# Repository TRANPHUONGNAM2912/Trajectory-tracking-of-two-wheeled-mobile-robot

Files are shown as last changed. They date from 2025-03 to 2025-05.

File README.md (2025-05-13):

<<<<<<< HEAD
# Điều Khiển Bám Quỹ Đạo Cho Robot Di Động Hai Bánh

## Tổng Quan
Dự án này tập trung vào việc thiết kế và đánh giá các bộ điều khiển bám quỹ đạo cho robot di động hai bánh vi sai. Nghiên cứu bao gồm việc phát triển và so sánh hiệu suất của nhiều phương pháp điều khiển như PID, SMC (Điều Khiển Trượt), ASMC (Điều Khiển Trượt Thích Nghi), Fuzzy Logic và Neural Network. Các bộ điều khiển được mô phỏng trong môi trường MATLAB/Simulink và sau đó được triển khai trên phần cứng thực tế thông qua mã nhúng C/C++ trên ESP32.

## Nội Dung Dự Án
- Mô hình hóa động học và động lực học của robot di động hai bánh vi sai
- Thiết kế các bộ điều khiển bám quỹ đạo:
  - Bộ điều khiển PID cổ điển
  - Bộ điều khiển trượt (SMC)
  - Bộ điều khiển trượt thích nghi (ASMC)
  - Bộ điều khiển logic mờ (Fuzzy Logic)
  - Bộ điều khiển mạng nơ-ron (Neural Network)
- Mô phỏng sử dụng MATLAB/Simulink
- Thiết kế mô hình phần cứng trên Solidworks
- Triển khai nhúng sử dụng ESP32
- So sánh hiệu suất giữa kết quả mô phỏng và thực nghiệm

## Cấu Trúc Thư Mục
- `Embedded_code/`: Chứa tất cả các bộ điều khiển cho ESP32
  - `NeuralNetwork.ino`: Triển khai bộ điều khiển mạng nơ-ron
  - `SMC.ino`: Triển khai bộ điều khiển trượt
  - `ASMC.ino`: Triển khai bộ điều khiển trượt thích nghi
  - `Fuzzy.ino`: Triển khai bộ điều khiển logic mờ
  - `PID_backstepping.ino`: Triển khai bộ điều khiển PID với backstepping
  - `GUI_CAR.py`: Giao diện Python để điều khiển và giám sát robot
- `MATLAB/`: Chứa các mô hình mô phỏng cho tất cả các bộ điều khiển
  - `NeuralNetwork/`: Mô phỏng bộ điều khiển mạng nơ-ron
  - `SMC/`: Mô phỏng bộ điều khiển trượt
  - `ASMC/`: Mô phỏng bộ điều khiển trượt thích nghi
  - `Fuzzy/`: Mô phỏng bộ điều khiển logic mờ
  - `PID/`: Mô phỏng bộ điều khiển PID
- `Solidworks/`: Chứa các mô hình CAD 3D của robot
- `docs/`: Tài liệu dự án và các bài báo nghiên cứu
  - `NeuralNetwork.pdf`: Tài liệu về bộ điều khiển mạng nơ-ron
  - `ITCA2024_NeuralNetwork.pdf`: Bài báo nghiên cứu về triển khai mạng nơ-ron
  - `VCCA2024_Fuzzy.pdf`: Bài báo nghiên cứu về triển khai logic mờ

## Yêu Cầu Phần Mềm
- MATLAB R2021B (hoặc cao hơn)
- Arduino IDE 2.xx (để lập trình ESP32)
- Solidworks 2022
- Python 3.x (cho ứng dụng giao diện)

## Yêu Cầu Phần Cứng
- Vi điều khiển ESP32
- Bộ điều khiển động cơ
- Động cơ DC có bộ mã hóa
- Khung cơ khí (theo thiết kế Solidworks)
- Nguồn điện

## Hướng Dẫn Cài Đặt
1. **Cài Đặt ESP32:**
   - Cài đặt board ESP32 của Espressif (phiên bản 2.0.17) trong Arduino IDE
   - Mở một trong các file điều khiển từ thư mục `Embedded_code/` trong Arduino IDE
   - Cập nhật SSID và mật khẩu WiFi trong mã
   - Tải mã lên ESP32

2. **Cài Đặt Giao Diện:**
   - Kết nối ESP32 và máy tính đến cùng một mạng WiFi (2.4GHz)
   - Ghi lại địa chỉ IP do ESP32 cung cấp sau khi kết nối
   - Cập nhật biến `ip_address` trong file `GUI_CAR.py`
   - Chạy ứng dụng giao diện Python

3. **Vận Hành:**
   - Sử dụng giao diện để bắt đầu/dừng robot
   - Giám sát hiệu suất và khả năng bám quỹ đạo trong thời gian thực

## Video Demo
- Xem demo: [Điều Khiển Bám Quỹ Đạo Cho Robot Di Động Hai Bánh](https://www.youtube.com/watch?v=6Xz11GfAjuo&t=38s)

## Lưu Ý Quan Trọng
- ESP32 và laptop phải kết nối cùng một mạng WiFi 2.4GHz
- Đảm bảo cài đặt tất cả các thư viện cần thiết cho ESP32 (WiFi, WebServer, MatrixMath)
- Nên giám sát mức pin trong quá trình hoạt động

## Giấy Phép
Dự án này được phân phối theo giấy phép MIT. Xem file LICENSE để biết thêm chi tiết.

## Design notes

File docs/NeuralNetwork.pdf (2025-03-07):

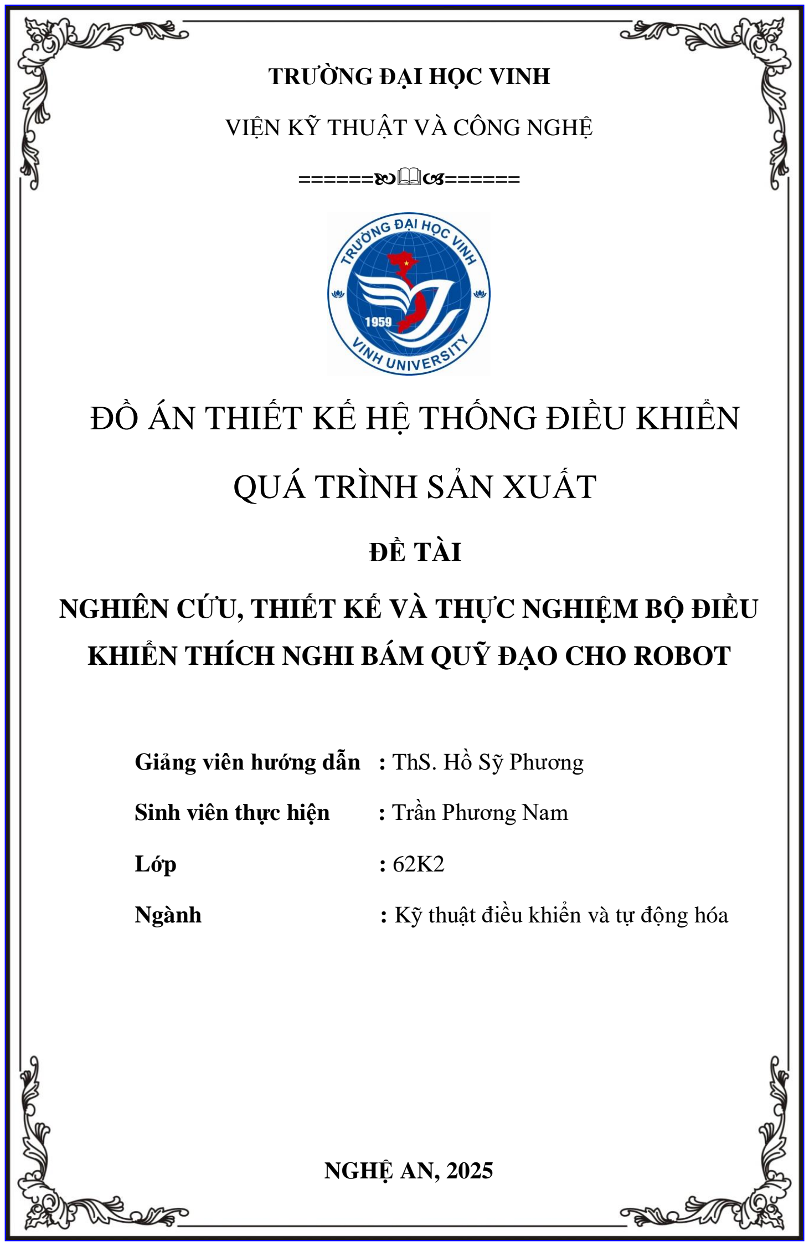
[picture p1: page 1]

TRƯỜNG ĐẠI HỌC VINH

VIỆN KỸ THUẬT VÀ CÔNG NGHỆ

============

## ĐỒ ÁN THIẾT KẾ HỆ THỐNG ĐIỀU KHIỂN

## QUÁ TRÌNH SẢN XUẤT

### ĐỀ TÀI

### NGHIÊN CỨU, THIẾT KẾ VÀ THỰC NGHIỆM BỘ ĐIỀU

### KHIỂN THÍCH NGHI BÁM QUỸ ĐẠO CHO ROBOT

Giảng viên hướng dẫn : ThS. Hồ Sỹ Phương

Sinh viên thực hiện | : Trần Phương Nam
Lớp | : 62K2
Ngành | : Kỹ thuật điều khiển và tự động hóa

NGHỆ AN, 2025

TRƯỜNG ĐẠI HỌC VINH | CỘNG HÒA XÃ HỘI CHỦ NGHĨA VIỆT NAM
VIỆN KT&CN | Độc lập – Tự do – Hạnh phúc

ĐỀ CƯƠNG THỰC HIỆN ĐỒ ÁN

Họ và tên sinh viên: Trần Phương Nam – 215752021610076

Ngành: Kỹ thuật điều khiển và tự động hóa

Đề tài: Nghiên cứu, thiết kế và thực nghiệm bộ điều khiển bám quỹ đạo cho robot.

### 1. Nhiệm vụ:

- Tìm hiều và xác định nội dung đồ án.
- Nghiên cứu mô hình toán học, động học, động lực học.
- Thiết kế bộ điều khiển, mô phỏng kiểm chứng bằng Matlab Simulink
- Lập trình, tiến hành thực nghiệm cho mô hình.
- Đánh giá kết quả thực nghiệm.
- Kết luận và hướng phát triển.

### 2. Ngày giao đồ án: Ngày 1 Tháng 9 năm 2024

### 3. Ngày hoàn thành đồ án: Ngày 10 Tháng 01 Năm 2025

Người hướng dẫn: ThS. Hồ Sỹ Phương

Nghệ An, Ngày ... Tháng ... Năm 202..

TRƯỞNG BỘ MÔN | NGƯỜI HƯỚNG DẪN

TRƯỜNG ĐẠI HỌC VINH | CỘNG HÒA XÃ HỘI CHỦ NGHĨA VIỆT NAM
VIỆN KT&CN | Độc lập – Tự do – Hạnh phúc BẢN TỰ ĐÁNH GIÁ

Nhóm trưởng: Trần Phương Nam

Đề tài: Nghiên cứu, thiết kế và thực nghiệm bộ điều khiển bám quỹ đạo cho robot.

| Phần đánh giá

Nghệ An, Ngày Tháng 01 Năm 2025 NHÓM TRƯỞNG

TT | Họ và tên MSSV | Nội dụng thực hiện | Kết quả | Đánh giá(%) | Ghi chú
1 | Trần Phương Nam 215752021610076 | - Nghiên cứu mô phỏng - Lập trình cho Robot -Thực nghiệm và tối ưu thuật toán | Hoàn thành | 100% | Nhóm trưởng

TRƯỜNG ĐẠI HỌC VINH | CỘNG HÒA XA HỘI CHỦ NGHĨA VIỆT NAM
VIỆN KT&CN | Độc lập – Tự do – Hạnh phúc

NHẬN XÉT CỦA NGƯỜI HƯỚNG DẪN

Họ và tên sinh viên: Trần Phương Nam – 215752021610076

Ngành: Kỹ thuật điều khiển và tự động hóa

Đề tài: Nghiên cứu, thiết kế và thực nghiệm bộ điều khiển bám quỹ đạo cho robot.

Nhận xét chung:

Phần đánh giá

TT | Họ và tên MSSV | Nội dụng thực hiện | Kết quả | Đánh giá(%) | Ghi chú
1 | Trần Phương Nam 215752021610076 | - Nghiên cứu mô phỏng - Lập trình cho Robot - Thực nghiệm và tối ưu thuật toán | | | Nhóm trưởng
- Ý thức thực hiện: |
- Nội dung thực hiện: |
- Hình thức trình bày: |
Tổng hợp kết quả( điểm bằng số và bằng chữ):
+Điểm chuyên cần: |
+Điểm giữa kỳ: |

Nghệ An, Ngày ... Tháng 01 Năm 2025 NGƯỜI HƯỚNG DẪN

MỤC LỤC

DANH MỤC HÌNH ẢNH

Hình 3.7 Tham số điều khiển được huấn luyện và chỉnh định theo điều kiện thực nghiệm

TÓM TẮT

Robot di động 2 bánh vi sai (DDMR) đã trở thành một nền tảng phổ biến trong các

ứng dụng công nghiệp và dịch vụ nhờ tính linh hoạt, dễ thiết kế và triển khai trong nhiều

môi trường khác nhau. Tuy nhiên, việc điều khiển chính xác quỹ đạo của robot trong thực

tế vẫn là một bài toán khó do sự xuất hiện của nhiễu và các yếu tố môi trường thay đổi

liên tục [1][2]. Các phương pháp điều khiển truyền thống như PID hay điều khiển trượt

(SMC) thường được sử dụng nhờ tính hiệu quả trong các tình huống tiêu chuẩn, nhưng

chúng lại phụ thuộc nhiều vào mô hình động lực học chính xác. Điều này dẫn đến hạn

chế trong việc xử lý các yếu tố bất định và biến đổi không dự đoán trước, đặc biệt khi hệ

thống hoạt động trong môi trường phức tạp [3][4].

Để vượt qua những thách thức này, mạng nơ-ron nhân tạo (ANN) đã được triển

khai trong các bộ điều khiển robot như một công cụ mạnh mẽ, nhờ khả năng học tập và

thích nghi với các điều kiện thay đổi. ANN có thể giảm sự phụ thuộc vào các mô hình

toán học phức tạp, cho phép robot tự động điều chỉnh các tham số điều khiển, từ đó cải

thiện hiệu suất và độ chính xác trong việc bám quỹ đạo [5][6]. Nhiều nghiên cứu đã

chứng minh ANN có khả năng ước lượng chính xác các tham số hệ thống, đồng thời xử

lý hiệu quả các yếu tố bất định và nhiễu động trong môi trường thực tế [7][8]. Tuy nhiên,

đa số các nghiên cứu này chỉ dừng lại ở mức mô phỏng, chưa được kiểm chứng đầy đủ

trên các hệ thống thực tế [9].

Trong đồ án này, nhóm thực hiện phát triển và kiểm chứng một bộ điều khiển

thích nghi dựa trên mạng nơ-ron dành cho DDMR. Bộ điều khiển được thiết kế để tự học

và điều chỉnh tham số động học chưa biết, từ đó tối ưu hóa khả năng bám quỹ đạo trong

môi trường có nhiễu và yếu tố biến động. Đặc biệt, bộ điều khiển không chỉ giúp giảm

thiểu sai số mà còn đảm bảo độ ổn định cao ngay cả trong điều kiện hoạt động khắc

nghiệt [10]. Kết quả thực nghiệm đã chứng minh bộ điều khiển đạt hiệu suất vượt trội so

với các phương pháp truyền thống, với khả năng duy trì tính chính xác và ổn định của hệ

thống trong nhiều tình huống khác nhau [11].

Nội dung đồ án được tổ chức thành 4 phần chính. Phần 1 trình bày chi tiết quá

trình mô hình hóa robot. Phần 2 đi sâu vào mô tả bộ điều khiển dựa trên mạng nơ-ron, tập

trung vào cách thức tự động chỉnh định tham số. Phần 3 phân tích kết quả thực nghiệm,

minh chứng hiệu quả của bộ điều khiển trong điều kiện thực tế. Cuối cùng, phần 4 kết luận và đề xuất các hướng phát triển trong tương lai, nhấn mạnh tiềm năng ứng dụng của

đồ án trong các hệ thống tự động hóa khác [12].

CHƯƠNG 1. MÔ HÌNH HOÁ ROBOT

### 1.1 Mô hình toán học

Cấu trúc của robot di động được thiết kế có bốn bánh xe. Hai bánh xe ở giữa là 2

bánh chủ động, được điều khiển bởi hai động cơ DC. Một bánh xe phía trước và sau thân

robot là 2 bánh thụ động. Cấu trúc robot được thể hiện trong Hình 1.1. Điểm G là trọng

tâm robot, 2 động cơ được sắp xếp đồng trục.

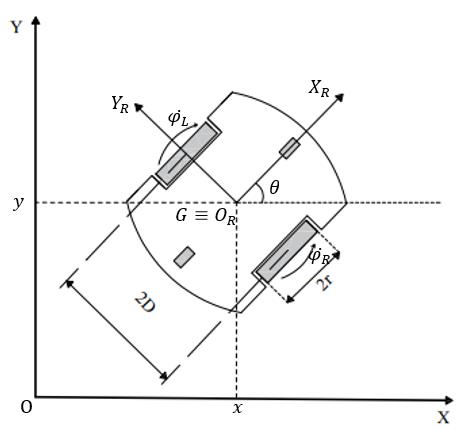
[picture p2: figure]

Hình 1.1 Cấu trúc robot di động

Hệ toạ độ tại điểm G{ORXRYR} gắn trên thân robot được gọi là hệ toạ độ robot

hoặc hệ toạ cục bộ vì hệ toạ độ này được dịch chuyển theo chuyển động của robot di

động. Hệ toạ độ còn lại {OXY} được gọi là hệ toạ độ quán tính hay hệ toạ độ cố định,

được sử dụng khi làm việc trên vị trí của robot. Hai hệ toạ độ này lần lượt được biểu diễn

như sau:

[ | ]
[ | ]

T
R | r | r | r
| | T
q | x y
q | x y

θ

| θ

ì
ï =
í
ï = î

(1)

Một ma trận biến đổi Rot(θ) được sử dụng để chuyển đổi giữa hệ toạ độ cố định

và hệ toạ độ robot:

1
( ) | ( ) R | R q | Rot | q | q Rot | q θ | θ
= | Þ = | (2)

Trong đó:

1

| cos | sin | 0
( ) | sin | cos | 0
| 0 | 0 | 1

Rot

| θ | θ
θ | θ | θ

é | ù -
ê | | ú
=
ê | | ú
ê | ú ë | û

(3)

### 1.2 Mô hình động học

Động học của robot liên quan đến mối quan hệ giữa vị trí, vận tốc, gia tốc và các

cấu trúc vật lý của nó. Bằng cách thay đổi vận tốc của hai bánh xe, quỹ đạo của robot có

thể thay đổi.
, φφR L

lần lượt là vận tốc quay của bên phải và bên trái. Ta có:

R | R
L | L
V | r
V | r φ
| φ

=
=

(4)

VR
và

VL

là vận tốc tuyến tính bánh xe phải và trái. Với bất ký trường hợp nào, v

và
ω

có thể được tính như sau:

( | )
2
( | )
2
R | L
R | L
V | V
v

V V D
ω

+
=
=

(5)

Từ (3) và (4), mối quan hệ vận tốc giữa hai toạ độ được biểu diễn như sau:

( | ) cos
2
| | cos | 0
( | )sin | sin | 0
2
0 | 1 ( | )

2

R | L
R | L
R | L
V | V

x
V | V | v
y

V V
D

θ
θ
θ | θ
ω
θ
é | ù +
ê | ú éù ê | ú é | ù êú | + | éù ê | ú ê | ú
= | = êú | êú ê | ú ê | úëû êú ê | ú ê | ú ëû | ë | û -
ê | ú ê | ú ë | û

(6)

Mô hình động học thuận của robot có thể được miêu tả như sau:

cos | 0
sin | 0 | ( ) ( )
0 | 1

x
v
y | S q V t

θ
θ
ω
θ
éù é | ù êú | éù ê | ú
= | = êú | êú ê | úëû êú ê | ú ëû ë | û

(7)

### 1.3 Mô hình động lực học

Phân tích động lực học của robot có thể được định nghĩa là kiểm tra mối quan hệ

giữa độ lớn mô-men xoắn hoặc độ lớn lực tác dụng lên bánh xe bởi bộ truyền động, vị trí,

vận tốc và gia tốc của robot theo thời gian. Sự khác biệt giữa mô hình động lực học và mô hình động học là mô hình động học chỉ xem xét chuyển động với các quan hệ hình

học chi phối hệ thống mà không xem xét các lực tác động đến chuyển động.

Theo [12], mô hình động lực học tính được như sau:

( ) | ( , ) | ( ) | ( )
( ) | ( )
M q q V q q q F q | G q | d
B q | A q τ

τ

τ | λ
+ | + | + | +
= | -

(8)

q, q˙ và q¨ lần lượt chỉ định các vectơ vị trí, vận tốc và gia tốc tương ứng. M(q) là

ma trận quán tính xác định dương đối xứng, V(q, q˙ ) là ma trận hướng tâm và Coriolis,

G(q) là lực hấp dẫn vectơ, τd biểu thị các nhiễu hoặc nhiễu không xác định giới hạn, bao

gồm cả động lực học phi cấu trúc không được mô hình hóa, B(q) là ma trận biến đổi đầu

vào, τ là vectơ mô-men xoắn đầu vào, A

τ
(q) là ma trận được liên kết với các ràng buộc

và λ là vectơ của các lực ràng buộc. Bỏ qua lực hấp dẫn G(q), ma sát của bánh xe được

truyền vào hệ có sai số được xác định trong mô hình động học nên
Fq()
bị bỏ qua, giá trị

nhiễu được cộng vào tín hiệu điều khiển của cơ cấu chấp hành nên ta bỏ qua trong mô

hình động. m

là khối lượng và
I

biểu thị mô men quán tính của robot, ta có:

00
( ) | 0 | 0 , ( ) 0, ( ) 0
0 | 0

m
M q | m | G q | F q
I
æ | ö ç | ÷
= | = | = ç | ÷ ç | ÷ è | ø

1

2

| cos | cos
1
Bq( ) | sin | sin | ,
r
| D | D
θ | θ
τ
θ θ τ
τ
é | ù | éù ê | ú
= | = êú ê | ú | ëû ê | ú ë | û -

1

2

3

| 0 | | sin
( , ) | 0 , | ( ) | cos
| 0 | | 0
T V q q | A q

θλ
λ | θ λ
λ
é ù | é | ù - | éù
ê ú | ê | úêú
= | = ê ú | ê | úêú
ê ú | ê | úêú ë û | ë | ûëû

(9)

Phương trình động lực học của robot được viết lại như sau:

M q q | B q | A q ( ) | ( ) | ( ) τ
= | - τ | λ | (10)

Ma trận S(q) được sử dụng để rút gọn. Ma trận S(q) là ma trận động học tịnh tiến

được sửa đổi liên quan đến khoảng cách giữa trọng tâm của robot và trục bánh xe, như đã

thấy trong phương trình động học tịnh tiến:

q S q = ()η | (11)

Ma trận gia tốc thu được bằng cách lấy đạo hàm thời gian phương trình (11) như

sau:

q | S q | S q = | + ( ) | ( ) η | η | (12)

Sử dụng phương trình (10) và (12), mô hình robot được sửa như sau:

M q S q | M q S q | B q | A q ( ) ( ) | ( ) ( ) | ( ) | ( ) τ η | η | τ | λ + | = | - | (13)

Nhân cả 2 vế cho ma trận biến đổi S

T
(q), ta có:
( ) ( ) ( ) | ( ) ( ) ( )
( ) ( ) | ( ) ( )
T | T
T | T
S q M q S q | S q M q S q
S q B q | S q A q τ
η | η
τ | λ

+

= | -

(14)

Ma trận S(q) nằm trong không gian rỗng của ma trận ràng buộc động học A(q),

có nghĩa là S

T
(q)A

T
(q) = 0. Vì vậy, phương trình (14) trở thành:
M q | V q q | B q ( ) | ( , ) | ( ) η | η | τ + | = | (15)

Các thuật ngữ mô hình động trong phương trình (15) có thể được trình bày như

sau:

0
( ) ( ) ( ) ( )
0

00
( , ) ( ) ( ) ( )
00
1 1 | 1
( ) | ( ) ( )

T

T

T

m
M q S q M q S q
I
V q q | S q M q S q
B q | S q B q
r D | D
| é | | ù
= | = ê | ú ë | û
| é | | ù
= | = ê | ú ë | û
| é | | ù
= | = ê | ú ë | û -

(16)

Sử dụng vận tốc trong phương trình (5), phương trình (15) có thể được chuyển đổi

thành dạng thay thế. Cấu trúc này trong phương trình (17) là mô hình phi tuyến.

1 | 1
2 | 2
1 | 1
0 | 1 | 1 1
0
m | v | v | rm | rm
I | D | D r | D | D
| | | rI | rI
τ | τ
ω | ω τ | τ
é | ù
ê | ú é | ù é ù | é | ù | é ù é ù | é ù
= | Þ | = ê | ú ê | ú ê ú | ê | ú | ê ú ê ú | ê ú ë | û ë û | ë | û | ë û - | ë û | ë û ê | ú -
ê | ú ë | û

(17)

Với mô hình phi tuyến, vận tốc tuyến tính và vận tốc góc thu được bằng cách sử

dụng phương trình (17).

CHƯƠNG 2. THIẾT KẾ BỘ ĐIỀU KHIỂN

Phương pháp điều khiển theo quỹ đạo thường được áp dụng trong các môi trường

đã biết và dựa trên động học của robot. Tuy nhiên, khi các yếu tố động lực như quán tính,

khối lượng hay vị trí khối lượng thay đổi, cần phải xem xét đến động lực học của robot.

Mục tiêu chính là giúp robot bám sát quỹ đạo đề ra, nhưng sự phức tạp của hệ thống cùng

các yếu tố bất định, nhiễu loạn hay lỗi cảm biến có thể gây ra sai lệch trong chuyển động.

Để giải quyết những thách thức này, bộ điều khiển được đề xuất có khả năng học hỏi từ

động lực học chưa biết, giúp robot bám theo quỹ đạo với độ chính xác cao trong môi

trường mô phỏng.
Cấu trúc bộ điều khiển đề xuất được thể hiện trên Hình 2.1 với sự tham gia của bộ điều

khiển động học với khả năng thích nghi nhờ sử dụng kiến trúc mạng nơ-ron thể hiện trong

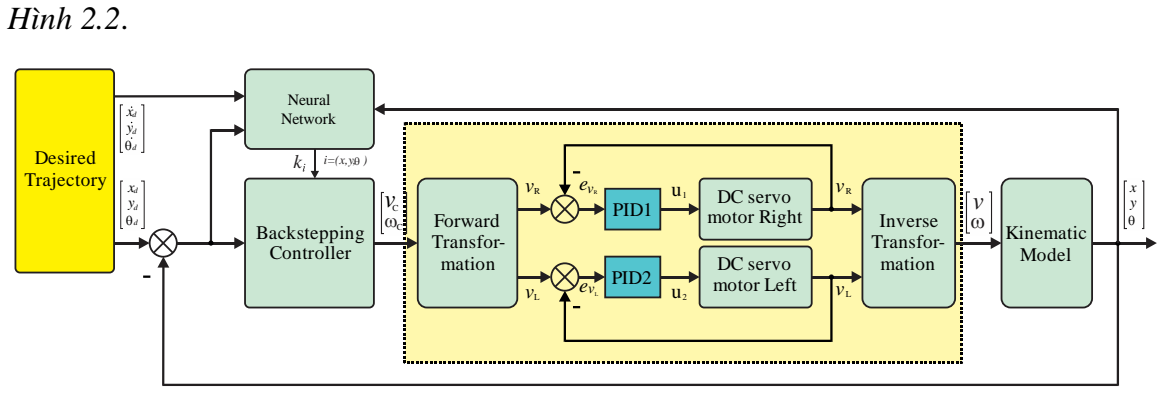
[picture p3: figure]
Hình 2.2.; Desired Trajectory; Backstepping Controller; Forward Transfor- mation; DC servo motor Right; DC servo motor Left; PID1; PID2; Kinematic Model; Inverse Transfor- mation; Neural Network; evR; evL

Hình 2.1 Sơ đồ cấu trúc bộ điều khiển đề xuất

### 2.1 Bộ điều khiển Backstepping

Với

[ ]

T
q | x y = | θ
và

[ ]

T
R | r | r | r q | x y = | θ

lần lượt là vị trí trong hệ toạ độ cố định và

hệ toạ độ robot. Sự khác biệt giữa q

và
R

q

cho các giá trị sai lệch về vị trí của robot trong

hệ tọa độ chuẩn. Phương trình sai lệch bám vị trí của robot được chỉ ra[18]:

cos | sin | 0
sin | cos | 0
0 | 0 | 1
| e | r
q | e | r
| e | r
| x | x | x
e | y | y | y
θ | θ
θ | θ
θ | θ θ
æö æ | öæ | ö -
ç÷ ç | ÷ç | ÷
= | = - | - ç÷ ç | ÷ç | ÷ ç÷ ç | ÷ç | ÷ èø è | øè | ø -
(18)

Đạo hàm cả 2 vế ta có:

cos
sin
e | e | r | e
q | e | e | r | e

r e

x | y | v v
e | y | x | v
ω | θ
ω | θ
θ | ωω
éù é | ù -+ êú ê | ú = | = | - | + êú ê | ú êú ê | ú ë | û -

ëû

(19)

Dựa trên cách tiếp cận được phát triển trong[18] luật điều khiển động học được áp

dụng như sau:

cos
( | sin )
c | r | e | x e
c | r | r | y e | e
v | v | K x
| v K y | Kθ

θ
ω | ω | θ
æö æ | ö +
ç÷ = ç | ÷ + | + èø è | ø
(20)

Kx,Ky và Kθ là các giá trị dương. Thông thường, để thiết kế các tham số này đòi

hỏi quá trình nhận dạng hệ thống với các thuật toán phức tạp. Ở đây nhóm đề xuất một

mạng nơ ron để điều chỉnh các tham số liên tục giúp robot có khả năng thích ứng tốt hơn

trước các nhiễu loạn và các nhân tố ảnh hưởng chưa biết.

### 2.2 Bộ điều khiển thích nghi dựa trên mạng Neural

Bộ điều khiển thích nghi dựa trên mạng nơ-ron theo phương pháp backstepping

được đề xuất cung cấp các tham số và hệ số thích nghi thay đổi theo quỹ đạo tham chiếu.

Cấu trúc điều khiển điều chỉnh các hệ số của bộ điều khiển dựa trên động học để tối thiểu

hóa hàm chi phí sau:

1 | 2 | 2 | 2
2
| x e | y e | e
J | g x | g y | g = | + | + ∑ | θθ | (21)

Ở đây,
,
x y

gg
, và

gθ

là các hệ số mạng nơ-ron. Các giá trị sai số được lấy từ

phương trình (18).

, | , K K K
x | y | θ

được xem là một phần của hàm chi phí ở trên và được tối

ưu hóa cũng như cập nhật dựa trên phương pháp gradient descent. Các hệ số điều khiển

động học được biểu diễn bởi vector α. Đạo hàm riêng của hàm chi phí đối với α được tính

như sau:

e | e | e | T | p
x e | y e | e | p
J | x | y | | e
g x | g y | g | e g θ
| | | θ
θ
α | α | α | α | α
∂ | ∂ | ∂ | ∂ | ∂
= | + | + | =
∂ | ∂ | ∂ | ∂ | ∂

(22)

với

α | K K K
x | y | θ = é | ù ë | û

Dạng ma trận của giá trị g được thể hiện như sau:

0 0

00

x

y

g
g | g

gθ

é | | ù
ê | | ú
= ê | | ú
ê | ú ë | û

(23)

Trong Phương trình (22), nếu
p

e

được thay thế bởi Phương trình (14):

( ( | )
e | r | c | c T
p | p | e
J | T q | q | q ge T | e | g T
α | α | α
∂ | ∂ | - | ∂
= | = - × × ×
∂ | ∂ | ∂

(24)

Vì vector

r q

là vị trí tham chiếu bao gồm các giá trị cố định, đạo hàm của nó bằng

0. Theo quy tắc chuỗi, phương trình sau có thể được viết:
c | c | c
| c
q | q | v
α | α v
∂ | ∂ | ∂
= | ×
∂ | ∂ | ∂

(25)

Sau khi có được Phương trình (25), biểu thức đạo hàm mong muốn trong Phương

trình (26) được viết như sau:

11 | 12
21 | 22
31 | 32

00
0 | sin
v | v
x
c
v | v
r y | r
v | v
Jac | Jac
q | e
Jac | Jac
v e v | e
Jac | Jac
α | θ
é | ù
∂ | é | ù ê | ú
= | × ê | ú ê | ú ∂ | ë | û ê | ú ë | û
(26)

Đạo hàm của hàm chi phí đối với các hệ số điều khiển

J
α

∂
∂

được viết lại như sau:

T | c
p | e | v
x | y
J | J | J | J | v e | g T Jac
α | α K K | Kθ
∂ | ∂ | ∂ | ∂ | ∂ é | ù
= | = - × × × | × ê | ú ∂ | ∂ | ∂ | ∂ | ∂ ê | ú ë | û
(27)

Biểu diễn đạo hàm của hàm chi phí theo các hệ số điều khiển ở dạng ma trận được

viết như sau:

[ | ]
11 | 12
21 | 22
31 | 32
| 00 | cos | sin | 0
0 | 0 | sin | cos | 0
00 | | 0 | 0 | 1

00
0 | sin

x

e | e | e | y
x | y
v | v
x
v | v
r y | r
v | v

g
J | J | J | J
x y | g
| K | K | K
g
| Jac | Jac
e
| Jac | Jac
v e v | e
| Jac | Jac

θ
θ

θ

θ | θ
θ | θ | θ
α
é | ù é | ù
∂ | ∂ | ∂ | ∂ é | ù | ê | ú ê | ú = | = - | × | × - ê | ú | ê | ú ê | ú ∂ | ∂ | ∂ | ∂ ê | ú ë | û | ê | ú ê | ú ë | û ë | û
é | ù é | ù ê | ú
× | × ê | ú ê | ú ë | û ê | ú ë | û

(28)

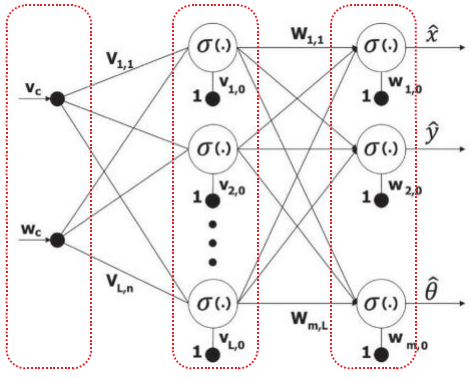
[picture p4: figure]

Hình 2.2 Cấu trúc các lớp của mạng nơ ron

Thuật toán tính ma trận Jacobian bằng mô hình mạng nơ-ron (NN): Các giá trị

trọng số ban đầu nên phù hợp nhất với mô hình. Trọng số được điều chỉnh bằng cách

huấn luyện mô hình sử dụng thuật toán lan truyền ngược (back propagation). Cần thiết

phải có các giá trị không chính xác để áp dụng thuật toán lan truyền ngược. Do đó, thuật

toán lan truyền tiến (forward propagation) được áp dụng trước tiên. Thuật toán này được

sử dụng để lấy dữ liệu dự đoán do NN tạo ra. Vì đây là dữ liệu dự đoán, nên tồn tại sự

khác biệt giữa giá trị ước tính và giá trị thực. Sự khác biệt này được sử dụng để xác định

giá trị sai số, lan truyền từ lớp đầu ra đến lớp đầu vào trên NN, dẫn đến "lan truyền

ngược" với các bước đạo hàm khác nhau .

Mô hình NN với hai lớp neuron được mô tả trong Hình 2.2.

Lớp đầu tiên của mô hình NN nhận L neuron, và lớp thứ hai nhận m neuron. Các

thuật ngữ sau được sử dụng để mô tả các tham số khác nhau của mạng nơ-ron như thể

hiện trong Hình 3:

- Vận tốc điều khiển động học
c

v
và

wc

là đầu vào cho NN.

•

ˆ
xy

ˆˆ
,,θ

là các đầu ra của NN.

- Ni
và

No

lần lượt là số lượng đầu vào và đầu ra của mạng nơ-ron.

- Nh

là số lượng neuron trong lớp ẩn.

- ζ
và

δ

là các hệ số học và tốc độ động lượng.

- σ
là hàm kích hoạt (activation function).
- Whi

là trọng số từ lớp ẩn đến lớp đầu vào.

- Who

là trọng số từ lớp đầu ra đến lớp ẩn.

Theo mô hình mạng nơ-ron được định nghĩa ở trên, mối quan hệ giữa đầu vào và đầu

ra của mạng được mô tả như sau:

0 | 0
1 | 1`
L | n
i | il | lj j | l | i
l | j
y | Woh | Whi x | v | w σ | σ
= | =
æ | ö æ | ö
= | + | + ç | ÷ ç | ÷ ç | ÷ è | ø è | ø ∑ | ∑ | (29)

Trong đó
i | m =1,2,...,

và

1, 2,..., L .

Hàm kích hoạt
σ

được chọn là hàm sigmoid, được biểu diễn trong phương trình (30):

1
1 e

ρ

σ -

=
+

(30)

Thuật toán lan truyền ngược cần đạo hàm của hàm kích hoạt. Đạo hàm của hàm sigmoid

đối với
ρ

được viết như sau:

( ) 2

1
( ) | ( ) 1 | ( )
(1 | ) p

d
f
d | e
σ ρ | σ ρ | ρ
ρ

= | = | -
+

(31)

Biểu thức
ρ

trong phương trình (30) là đại diện cho tích của trọng số và giá trị

neuron đến lớp mong muốn.

Thuật toán lan truyền ngược (Back Propagation) là một thuật toán điều chỉnh trọng

số dựa trên phương pháp gradient descent. Cập nhật trọng số được thực hiện như sau:

() ( | 1) | ( )
() ( | 1) | ( )
il | il
il
lj | lj
il

Ek W k W k
W
Ek V k V k
V

ζ

ζ

ì | ∂
+ = | - ï
ï | ∂
í
∂ ï | + = | - ï | ∂ î

(32)

Tín hiệu đầu ra được cung cấp như một tham chiếu cho mạng nơ-ron, và sự khác

biệt giữa tín hiệu đầu ra này và đầu ra
()i

y

do mạng nơ-ron tạo ra được coi là lỗi (error).

Các trọng số được thay đổi theo chu kỳ cho đến khi lỗi được tối thiểu hóa bởi mạng.

Lỗi được tính như sau:

12 ( ) | ( ) y ( ) i | i | i e k | Y k | k = | - | (33)

Trong đó:

() [ | ]

T
Y k | x | y i | A | A | A
= | α | (34)

Sử dụng hàm lỗi, hàm chi phí được tính như sau:

1 | 2
( ) | ( )
2

E k e k =
i

(35)

Các gradient yêu cầu của hàm chi phí E(k) theo trọng số được xác định bằng cách

sử dụng quy tắc dây chuyền (chain rule).

( | ) | ( | )
2 | 2
2 | 1 | 1 | 2
1 | 1
( 1) | ( ) | ( )
W
( ) | W | ( ) | ( )
i | i | l | l | i | i
il
m | m
i | i | il | l | j | j | l | i | i | il
i | i il

E
e | u | z | z | u e

E
u e | u | x | x | u | u e W
V
σ | σ
σ | σ | σ | σ
= | =

∂
= | × - × | × | = - é | ù ′ | ′ ë | û ∂
∂ | é | ù
= | - | × | × | × | = - | + ′ | ′ | ′ | ′ ê | ú ∂ | ë | û ∑ | ∑

(36)

Trong đó, zl là đầu ra hàm sigmoid của nơ ron l ở lớp ẩn. Ma trận Jacobian được

xác định như sau:

ˆ | ˆ | ˆ | ˆ ( ) | ( | 1) | ( ) | ( | 1)
( ) | ( | 1) | ( ) | ( | 1)
ˆ | ˆ | ˆ | ˆ ( ) | ( | 1) | ( ) | ( | 1)
( ) | ( | 1) | ( ) | ( | 1)
ˆ | ˆ | ˆ | ˆ ( ) | ( | 1) | ( ) | ( | 1)
( ) | ( | 1) | (
c | c | c | c | c | c

v
c | c | c | c | c | c
c | c | c | c | c
x | x | x t | x t | x t | x t
v | v t | v t | t | t
y | y | y t | y t | y t | y t Jac
v | v t | v t | t | t
| | t | t | t | t
v | | v t | v t
| ω | | | ω | ω
| ω | | | ω | ω
θ | θ | α | α | α | α
| ω | | | ω
é | ù ∂ | ∂ | - | - | - | - ê | ú ∂ | ∂ | - | - | - | - ê | ú
ê | ú ∂ | ∂ | - | - | - | -
= | = ê | ú ∂ | ∂ | - | - | - | - ê | ú
ê | ú ∂ | ∂ | - | - | - | - ê | ú ë | û ∂ | ∂ | - | - | ) | ( | 1)

c

t | t ω
é | ù
ê | ú
ê | ú
ê | ú
ê | ú
ê | ú
ê | ú
ê | ú ë | û - | -

(37)

Thông qua mạng nơ ron, bộ điều khiển động học trong phương trình (20) thay đổi

các giá trị điều chỉnh và thích nghi để làm cho hàm chi phí bằng 0 theo phương pháp

gradient descent như sau:

( ) | ( | 1)
( ) | ( | 1)
( ) | ( | 1)
x | x | x
y | y | y
k t | k t | k
k t | k t | k
k t | k t | k θ | θ | θ
ì | = | - + Δ ï
í | = | - + Δ
ï
î | = | - + Δ

(38)

Trong đó, sự thay đổi của các hệ số được tính toán theo các phương trình sau:

J
k

ζ

∂
Δ = -

Các hệ số

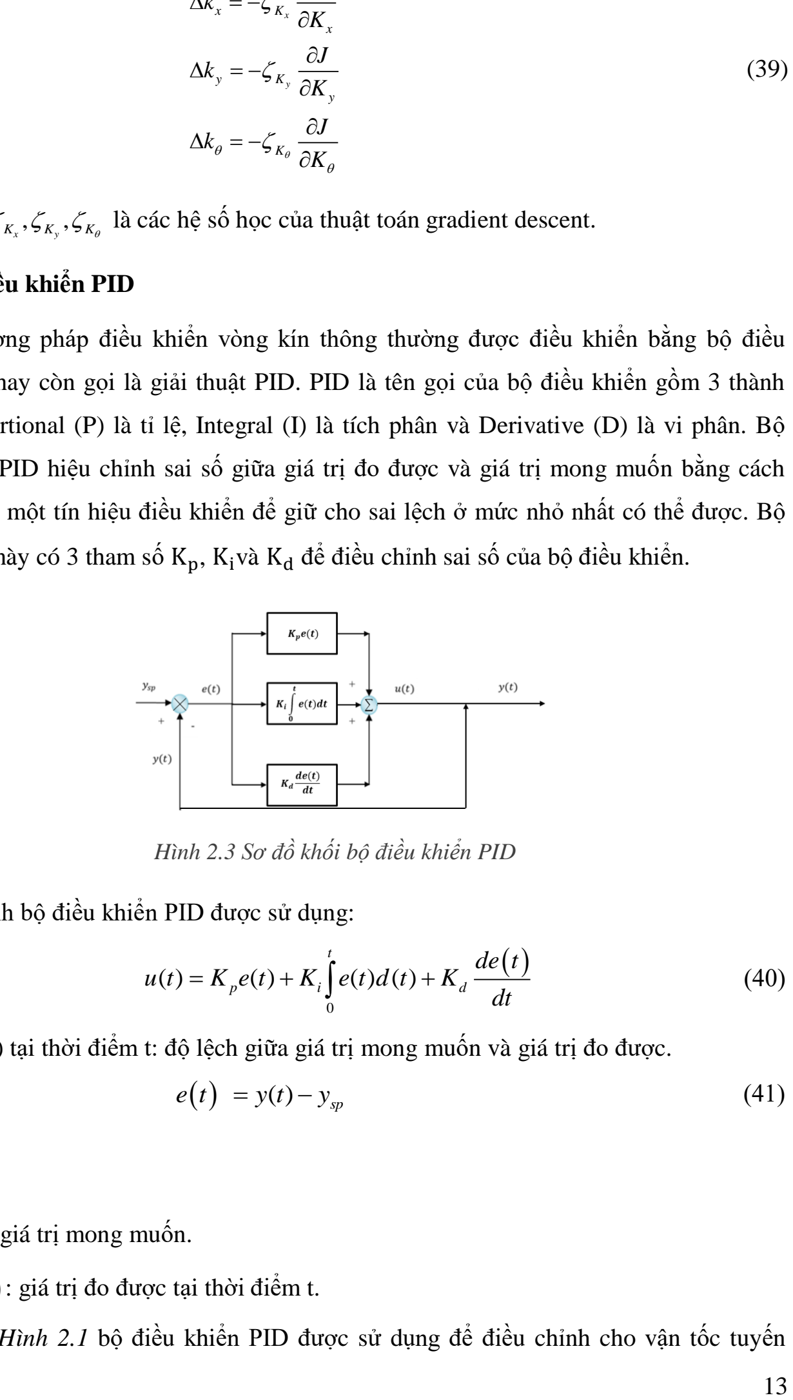
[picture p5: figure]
Hình 2.3 Sơ đồ khối bộ điều khiển PID; : giá trị đo được tại thời điểm t.

, | , K | K | K x | y | θ

ζ ζ ζ

là các hệ số học của thuật toán gradient descent.

### 2.3 Bộ điều khiển PID

Phương pháp điều khiển vòng kín thông thường được điều khiển bằng bộ điều

khiển PID hay còn gọi là giải thuật PID. PID là tên gọi của bộ điều khiển gồm 3 thành

phần Proportional (P) là tỉ lệ, Integral (I) là tích phân và Derivative (D) là vi phân. Bộ

điều khiển PID hiệu chỉnh sai số giữa giá trị đo được và giá trị mong muốn bằng cách

tính toán ra một tín hiệu điều khiển để giữ cho sai lệch ở mức nhỏ nhất có thể được. Bộ

điều khiển này có 3 tham số Kp, Kivà Kd để điều chỉnh sai số của bộ điều khiển.

Phương trình bộ điều khiển PID được sử dụng:

Sai lệch e(t) tại thời điểm t: độ lệch giữa giá trị mong muốn và giá trị đo được.

Trong đó :

+
sp

y

: giá trị mong muốn.

+

yt( )

Theo Hình 2.1 bộ điều khiển PID được sử dụng để điều chỉnh cho vận tốc tuyến tính và vận tốc góc của robot bám với giá trị mong muốn dựa vào độ sai lệch. Từ đó điều

khiển 2 động cơ gắn với 2 bánh chủ động của robot. Độ sai lệch được tính toán trong bộ

điều khiển PID là độ lệch giữa vận tốc đặt với vận tốc thực tế.

Có nhiều phương pháp xác định tham số của bộ điều khiển PID, trong bài báo này

nhóm tác giả sử dụng phương pháp Ziegler-Nichols thứ 2.

Các bước xác định thông số PID cho hệ thống theo phương pháp Ziegler–Nichols

thứ 2:

+ Đầu tiên đặt Ki = 0 và Kd = 0.

+ Chỉ sử dụng tác động khuếch đại, tăng Kp từ 0 tới một giá trị tới hạn Kcr, tại đó

đầu ra của hệ thống có dạng dao động điều hoà.

+ Xác định Kp và chu kỳ dao động Pcr bằng thực nghiệm.

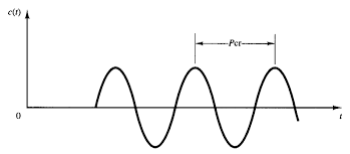
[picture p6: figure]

Hình 2.4 Chu kỳ dao động Pcr

Xác định các tham số Kp, Kivà Kd của bộ điều khiển theo bảng sau:

Type of Controller | K p | Ki | Kd
P | 0.5K cr | 0 | 0
PI | 0.45K cr | 0.85P cr | 0
PID | 0.6K cr | 0.5P cr | 0.125P cr

Bảng 2.1 Phương pháp Ziegler–Nichols

Tính toán Kivà Kd của hệ thống dựa vào Pcr, từ đó tìm được tham số của bộ điều

khiển PID. Sau quá trình thực nghiệm, các giá trị của bộ điều khiển tìm được như sau:

0.02, | 0.00015, | 0.01 K | K | K p | i | d
= | = | =

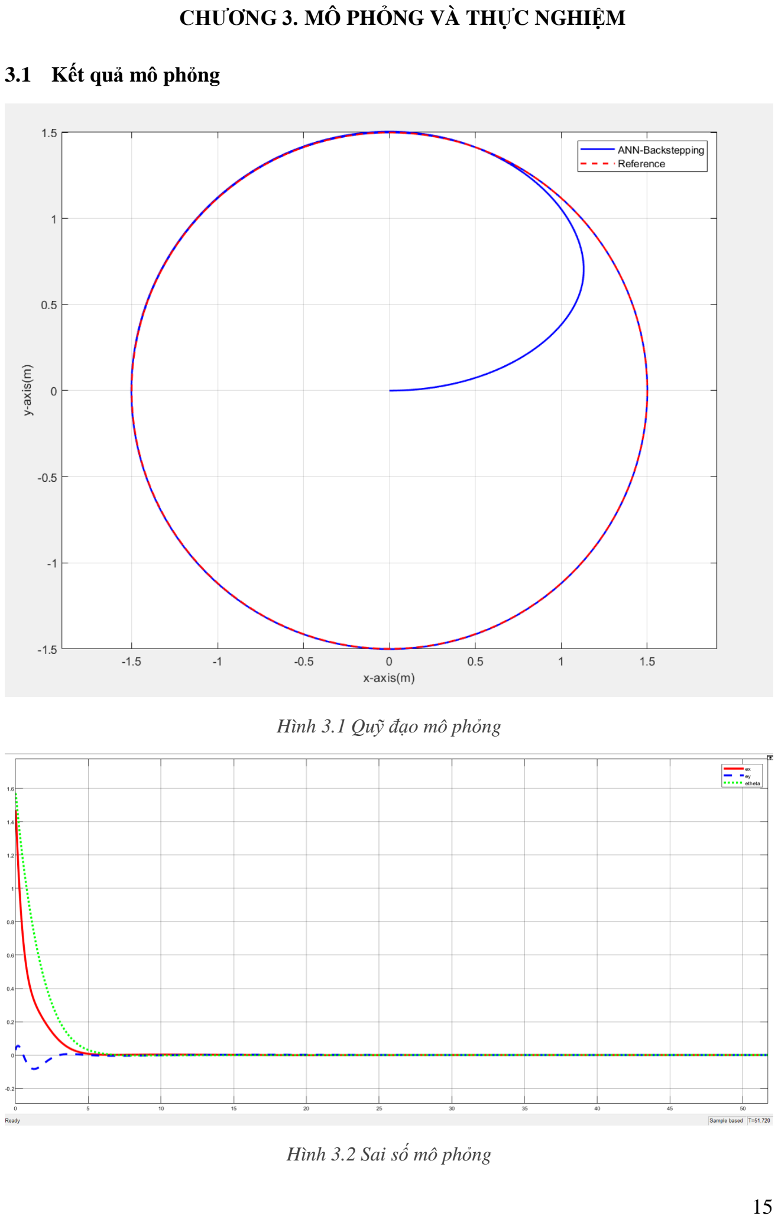
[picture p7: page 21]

CHƯƠNG 3. MÔ PHỎNG VÀ THỰC NGHIỆM

### 3.1 Kết quả mô phỏng

Hình 3.1 Quỹ đạo mô phỏng

Hình 3.2 Sai số mô phỏng

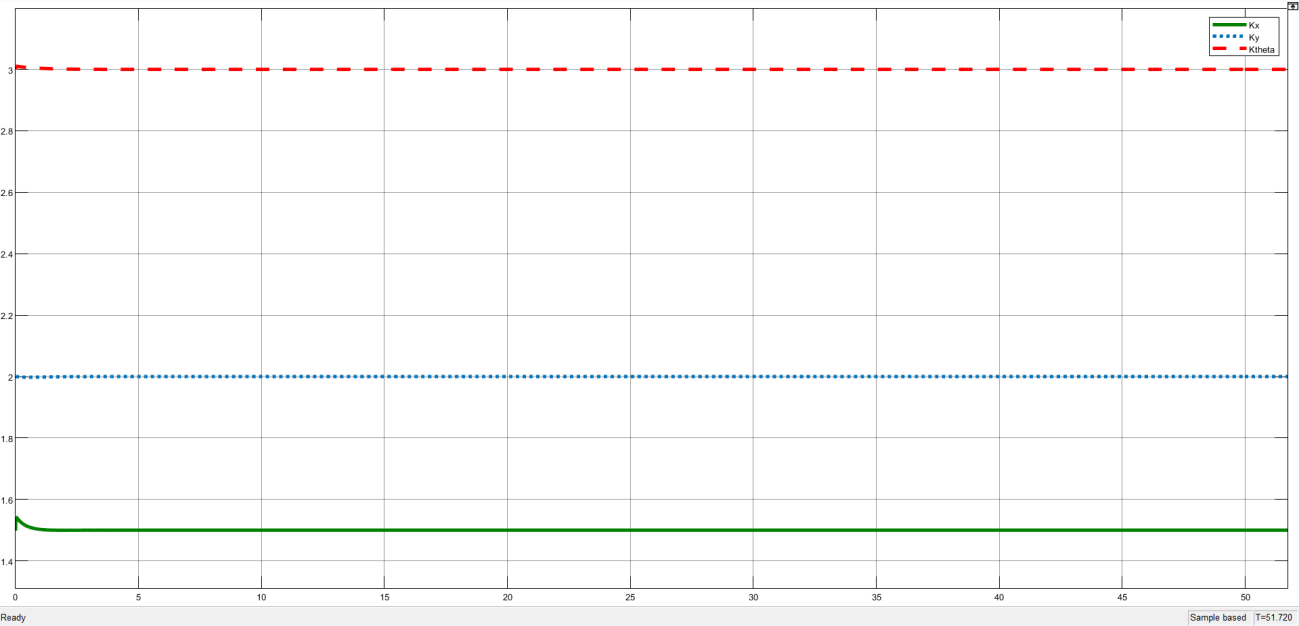
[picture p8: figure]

Hình 3.3 Các tham số được tinh chỉnh

### 3.2 Kết quả thực nghiệm

Trong phần này, chúng tôi thực hiện kiểm chứng bộ điều khiển đề xuất trong môi

trường thực nghiệm. Vị trí ban đầu của robot được đặt tại gốc tọa độ (0, 0, 0); Quỹ đạo

đặt là hình tròn được biểu diễn bởi phương trình (23):

sin( )
; | 1.25 , | 0.23rad/ s
cos( )

d

d

x | R | t
R | m
y | R | t ω
ω
| | ω

ì =
í | = | =
î =

(42)

Tham số của bộ điều khiển PID cho bộ phận truyền động được chọn dựa trên

phương pháp Ziegler–Nichols thứ 2: Kp = 0.002, Ki = 0.00015, Kd = 0.01. Khoảng cách giữa 2 bánh xe là 2D=0.38m, bán kính bánh xe: r=0.1m. Bộ điều khiển trung tâm được

sử dụng là ESP32, động cơ DC servo được sử dụng ở đây là Planet 24VDC-60W với 13 xung encoder. Mạch XD-160D là mạch diver để điều khiển động cơ DC.

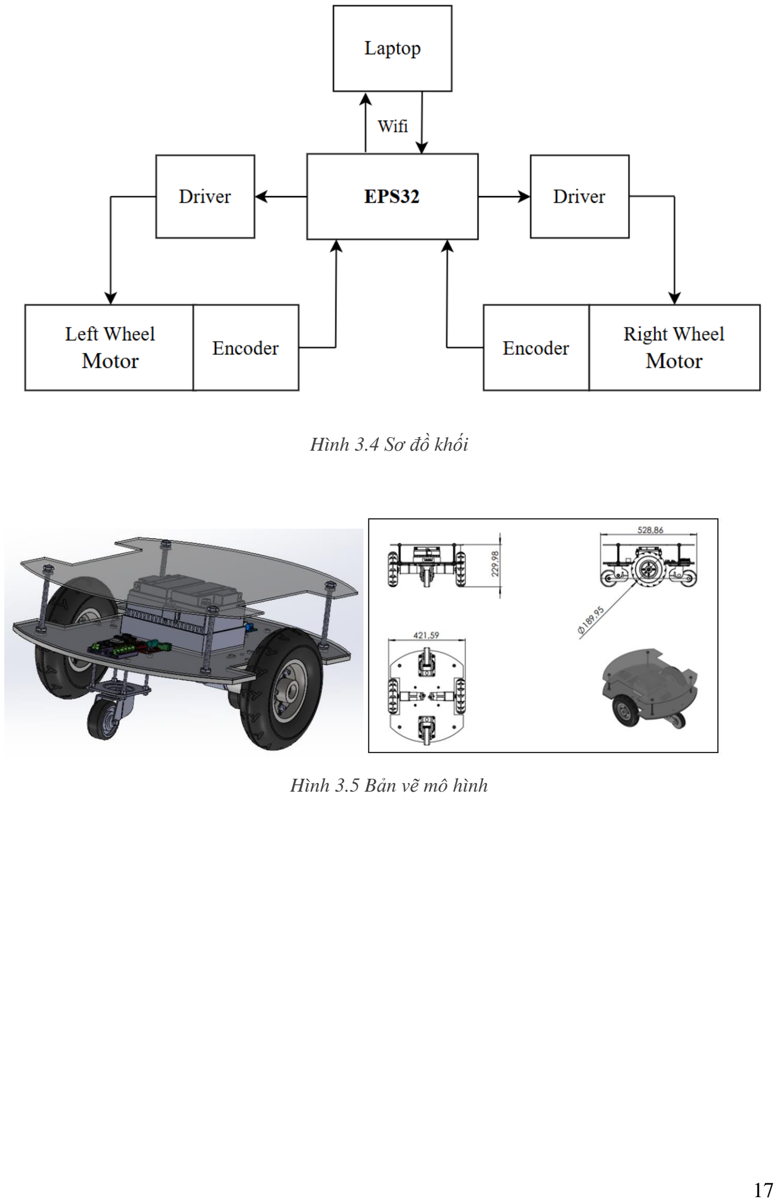
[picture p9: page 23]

Hình 3.4 Sơ đồ khối

Hình 3.5 Bản vẽ mô hình

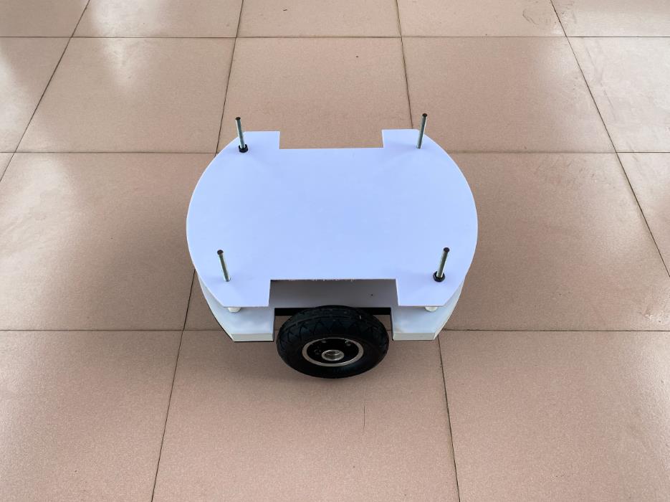
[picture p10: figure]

Hình 3.6 Mô hình thực nghiệm

Bộ thông số của mạng nơ ron:

Trọng số từ lớp đầu vào đến lớp ẩn.

Whi = [-6.4855 -4.0100 -4.5498;

-6.5890 -4.7984 -2.1504;

-6.5339 -3.9266 -4.3257;

-7.4260 -3.7515 -2.3720;

-6.3217 -4.2807 -3.3511;

-6.1753 -4.2071 -3.1082;

-8.9702 -5.8552 -4.7596;

-7.3099 -6.6322 -4.5009;

-6.2155 -5.9031 -5.4120;

-5.9862 -3.5501 -3.1355;

-5.9129 -4.1946 -3.8804;

-6.3110 -4.0644 -2.8849;

-6.2365 -2.9500 -2.3163;

-8.2328 -6.5682 -3.4148;

-7.1986 -3.6066 -2.8832;

-5.9831 -3.4436 -3.6779;

-6.3094 -3.8544 -3.2696;

-6.2915 -5.4654 -4.1758;

-6.5584 -4.4558 -3.2127;

-5.8346 -3.3768 -2.5838];

Trọng số từ lớp ẩn đến lớp đầu ra.

Woh= [0.0188 -1.9734 0.6255 0.4932 -0.5925 -0.4435 1.0799 0.3705 -0.1926 -1.1629

-0.0350 -0.9390 0.3647 -0.6056 0.5726 -0.1639 -1.3403 -1.5193 -1.6494 -1.8132

-0.2483;

-0.0693 1.2123 1.3129 1.6006 0.7402 1.1716 1.5867 3.1500 2.3577 3.3629 2.4780 2.6302 2.9674 0.7661 1.5265 2.0676 1.7297 4.0159 2.3748 2.4173 2.9054;

6.3216 3.3388 1.4826 -0.2754 -2.1694 -0.7430 -2.2963 -4.7001 -4.6418 -4.0895 -4.7556 -4.6468 -4.9112 -5.4908 -3.4376 -4.7539 -4.9947 -4.5363 -5.4131 -3.7736 -4.9652].

Số lượng đầu vào mạng nơ ron: Ni=2.

Số lượng đầu ra mạng nơ ron: No=3.

Số nơ ron trong lớp ẩn: Nh=20.

Hệ số tốc độ học: 0.7

Hệ số động lượng: 0.9

Kết quả thực nghiệm:

Video quá trình theo dõi và bám quỹ đạo của robot được thể hiện trong link đính kèm:

https://drive.google.com/drive/folders/1BHqT3GcOgGo_uNxxXz5bmAFDBDSqFcw2

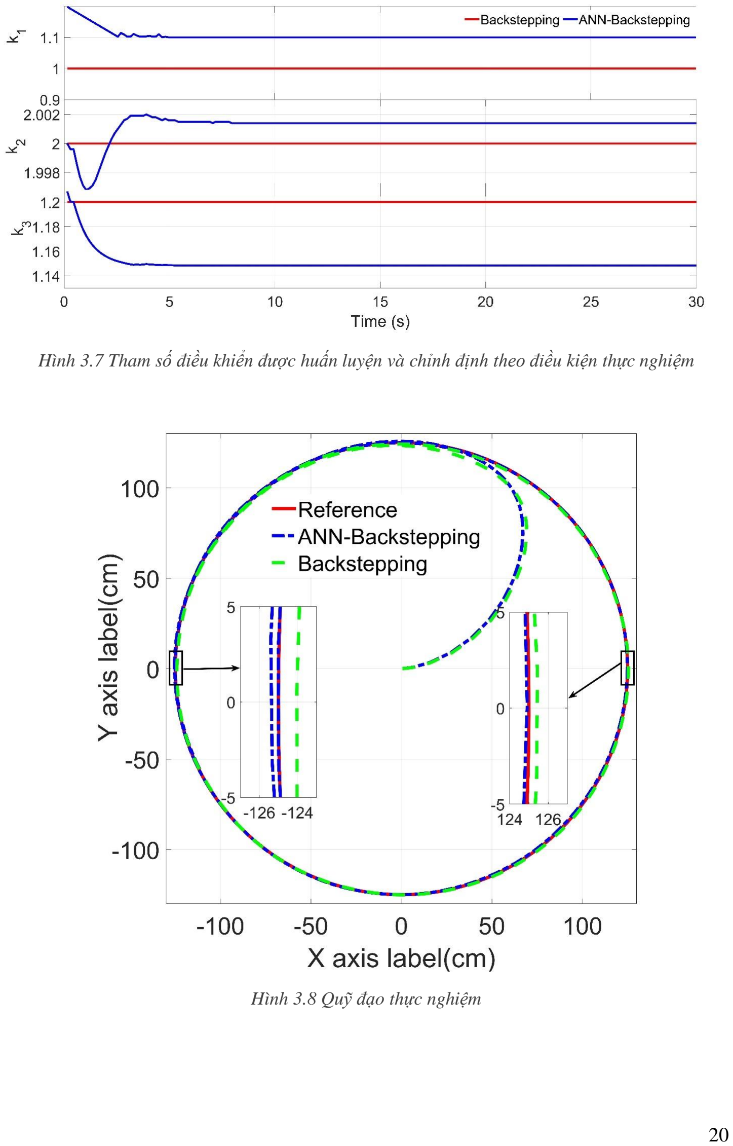
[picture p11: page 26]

Hình 3.7 Tham số điều khiển được huấn luyện và chỉnh định theo điều kiện thực nghiệm

Hình 3.8 Quỹ đạo thực nghiệm

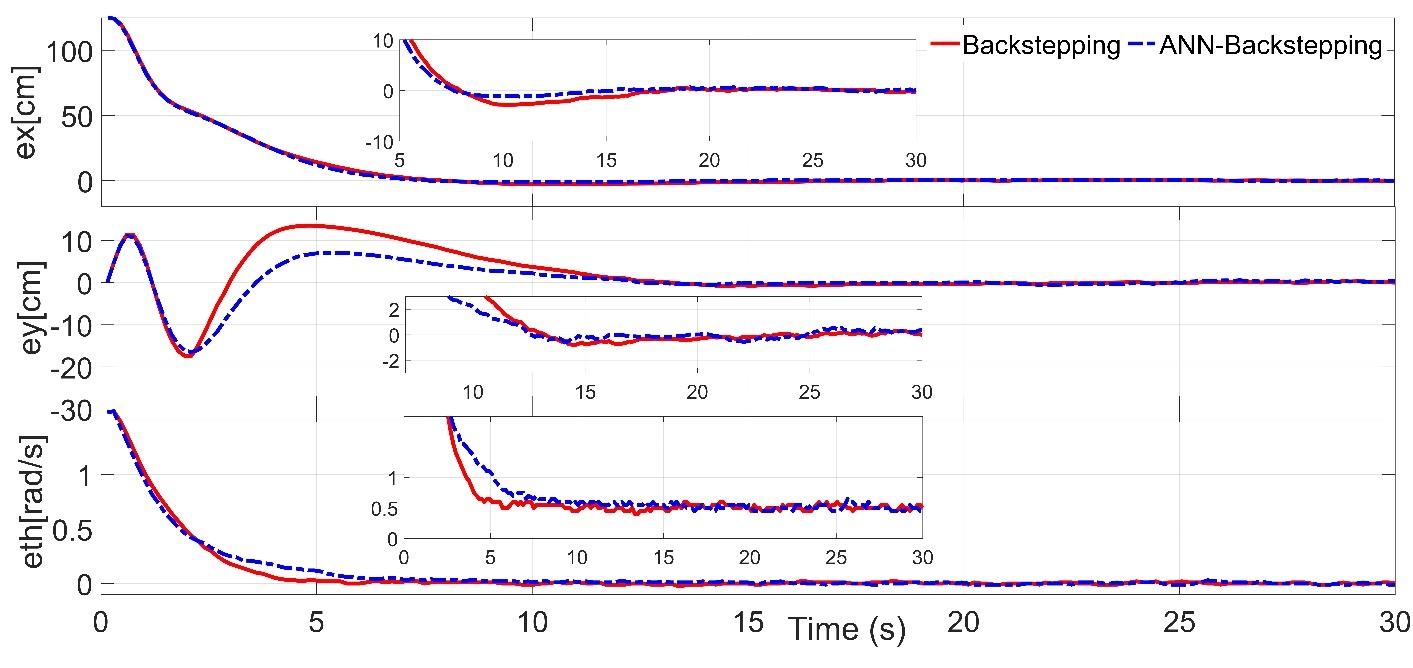
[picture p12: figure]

Hình 3.9 Sai lệch đo được trong quá trình theo dõi quỹ đạo đặt

Các tham số điều khiển thay đổi liên tục trong quá trình thực nghiệm (Hình 3.7), đảm

bảo rằng robot có thể phản ứng nhanh chóng với các biến động từ môi trường và duy trì

sự ổn định trong quá trình bám quỹ đạo. Điều này khẳng định khả năng tự học và thích

nghi của bộ điều khiển dựa trên mạng nơ-ron.

Sai lệch bám rất nhỏ và không có sự dao động lớn trên Hình 3.9, chứng minh rằng

mạng nơ-ron đã giúp điều chỉnh và bù trừ sai lệch một cách hiệu quả, giúp duy trì sự ổn

định của robot trong suốt quá trình vận hành. Từ Hình 3.8, có thể thấy rằng sai số bám

quỹ đạo của robot trung bình là 2.5%, với sai số tối đa trong các thử nghiệm là 3.2%.

Nguyên nhân của các sai số này chủ yếu đến từ nhiễu ngẫu nhiên trong môi trường thực

nghiệm và sự thay đổi bất thường trong điều kiện mặt đất. Tuy nhiên, nhờ khả năng tự

học của mạng nơ-ron, bộ điều khiển đã nhanh chóng điều chỉnh tham số và giảm thiểu sai

số xuống mức thấp nhất. Kết quả này cho thấy robot có thể thích ứng và duy trì độ chính

xác cao trong điều kiện môi trường thực nghiệm.

Kết quả thực nghiệm cũng cho thấy bộ điều khiển mạng nơ-ron thích nghi đạt hiệu

suất cao hơn so với Backstepping trong điều kiện thực tế:

Bộ điều khiển mạng nơ-ron có sai số bám quỹ đạo trung bình thấp hơn so với

Backstepping, với mức sai số trung bình là 2.5% so với 3.8% của Backstepping.

Thời gian hội tụ của bộ điều khiển mạng nơ-ron cũng ngắn hơn, trung bình 5 giây,

trong khi Backstepping cần 7 giây để đạt độ ổn định. Điều này cho thấy khả năng phản

ứng nhanh hơn của mạng nơ-ron đối với các thay đổi trong điều kiện môi trường.

CHƯƠNG 4. KẾT LUẬN VÀ HƯỚNG PHÁT TRIỂN

### 4.1 Kết luận

Trong đồ án này, nhóm đã phát triển và kiểm chứng một bộ điều khiển thích nghi dựa

trên mạng nơ-ron cho WMR trong môi trường thực nghiệm. Bộ điều khiển này có khả

năng tự học và thích nghi với các thay đổi của môi trường, giúp cải thiện đáng kể hiệu

suất bám quỹ đạo và giảm sự phụ thuộc vào các mô hình động lực học phức tạp. Kết quả

thực nghiệm đã cho thấy bộ điều khiển không chỉ đảm bảo độ chính xác cao trong quá

trình bám quỹ đạo mà còn giúp robot hoạt động ổn định trong môi trường thực tế ngay cả

khi hiểu biết về động lực học là hạn chế.

Việc sử dụng mạng nơ-ron để dự đoán và điều chỉnh các tham số điều khiển trong

thời gian thực đã chứng minh hiệu quả vượt trội, với sai số trong quá trình bám quỹ đạo

được giảm thiểu tối đa. Các kết quả từ Hình 3.7,3.8,3.9 cho thấy robot đã bám sát quỹ

đạo với sai số rất nhỏ, đồng thời bộ điều khiển đã tự điều chỉnh linh hoạt để đảm bảo tính

ổn định trong toàn bộ quá trình vận hành. Đồ án này là tiền đề cho nhóm phát triển các hệ

thống điều khiển thông minh trong thời gian tới, khi khả năng tự học và thích nghi là yếu

tố then chốt để đối phó với các thách thức từ môi trường thực tế.

### 4.2 Hướng phát triển

Để tiếp tục nâng cao hiệu suất và khả năng ứng dụng của robot di động, các hướng

phát triển trong tương lai có thể bao gồm:

- Thử Nghiệm Các Bộ Điều Khiển Mới: Để đánh giá hiệu quả và ổn định của hệ

thống, có thể thêm các bộ điều khiển tiên tiến như Model Predictive Control

(MPC) và các bộ điều khiển phi tuyến. Những bộ điều khiển này có thể giúp tối ưu

hóa quá trình điều khiển, cải thiện độ chính xác và khả năng dự đoán của robot di

động trong các điều kiện môi trường phức tạp.

- Tích Hợp Công Nghệ Xử Lý Ảnh: Nâng cao độ chính xác định vị bằng cách tích

hợp công nghệ xử lý ảnh hoặc sử dụng thuật toán Kalman Filter kết hợp GPS và

IMU. Điều này sẽ giúp robot xác định vị trí một cách chính xác hơn, đặc biệt trong

các môi trường có nhiều nhiễu loạn hoặc thay đổi liên tục.

- Nâng Cấp Phần Cứng: Để xử lý dữ liệu phức tạp và yêu cầu tính toán cao, có thể

nâng cấp phần cứng sử dụng trong hệ thống điều khiển như STM32 hoặc

Raspberry Pi. Những nâng cấp này sẽ cải thiện khả năng xử lý của hệ thống, đảm

bảo robot có thể hoạt động mượt mà và hiệu quả hơn trong các ứng dụng thực tế.

Những hướng phát triển này không chỉ giúp nâng cao chất lượng và hiệu quả của

robot di động mà còn mở ra những cơ hội ứng dụng mới trong nhiều lĩnh vực khác nhau,

từ công nghiệp đến dịch vụ và nghiên cứu khoa học.

TÀI LIỆU THAM KHẢO

[1] F. N. Martins, W. C. Celeste, R. Carelli, M. Sarcinelli-Filho, “A neural network-based adaptive controller for trajectory tracking of wheeled mobile robots,” IEEE Transactions on Neural Networks, vol. 19, no. 5, pp. 1178–1188, 2008.
[2] S. Li, Y. Wang, Y. Luo, "Robust adaptive control for wheeled mobile robots using neural networks," Journal of Intelligent & Robotic Systems, vol. 50, pp. 169–183, 2007.
[3] L. Li, T. Wang, Y. Xia, and N. Zhou, "Trajectory tracking control for wheeled mobile robots based on nonlinear disturbance observer with extended Kalman filter," Journal of the Franklin Institute, vol. 357, no. 15, pp. 8491–8507, 2020
[4] Štefek, V. T. Pham, V. Krivanek, and K. L. Pham, "Optimization of Fuzzy Logic Controller Used for a Differential Drive Wheeled Mobile Robot," Applied Sciences, vol. 11, no. 13, pp. 6023, 2021.
[5] P. Panahandeh, K. Alipour, B. Tarvirdizadeh, A. Hadi, “A kinematic Lyapunov-based controller to posture stabilization of wheeled mobile robots,” Mechanical Systems and Signal Processing, vol. 134, p. 106319, 2019.
[6] Y. Guo, "Fuzzy control and neural network-based trajectory tracking for non-holonomic mobile robots," Journal of Control Engineering and Technology, vol. 12, no. 2, pp. 189–196, 2019.
[7] M. Abdollahi, M. M. Baygi, M. A. Ahmadi, “Trajectory tracking control for mobile robots with neural network disturbance estimation,” International Journal of Robotics and Automation, vol. 33, pp. 129–136, 2015.
[8] Rossi, M. Milani, “Trajectory tracking via robust adaptive control of a non-holonomic mobile robot,” Journal of Dynamic Systems, Measurement, and Control, vol. 140, 2018(2020-(J)_Controlling wh…).
[9] Q. V. Dang, I. Nielsen, S. Bøgh, G. Bocewicz, “Modelling and scheduling autonomous mobile robot for a real-world industrial application,” IFAC Proceedings Volumes, vol. 46(9), pp. 2098–2103, 2013.
[10] Pazderski, “Application of transverse functions to control differentially driven wheeled robots using velocity fields,” Bulletin of the Polish Academy of Sciences: Technical Sciences, vol. 64.4, 2016.
[11] L. Armesto, V. Girbés, A. Sala, M. Vicente, “Adaptive tracking for wheeled mobile robots using fuzzy logic,” International Journal of Approximate Reasoning, vol. 45, pp. 163–179, 2018.
[12] H. S. Phuong, N. M. Tien, N. D. Tan, M. T. Anh and D. D. Tu, "Proposal of a Fault-tolerant controller for wheeled mobile robots with faulty actuators", 12th International Conference on Control, Automation and Information Sciences (ICCAIS), pp. 507-512, 2023.

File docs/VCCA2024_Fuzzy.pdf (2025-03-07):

Hội nghị - Triển lãm quốc tế lần thứ 7 về Điều khiển và Tự động hoá | VCCA-2024

## Thiết kế, triển khai và kiểm chứng Bộ điều khiển thích nghi mờ cho Robot di động có bánh xe bám quỹ đạo

## Design, Implementation and Verification an Adaptive Fuzzy logic controller for Trajectory Tracking in Wheeled Mobile Robots

Hồ Sỹ Phương¹

, Trần Phương Nam¹

, Mai Thế Anh¹
, Dương Đình Tú¹

, Lê Văn Chương¹
, Phan Văn Vỹ, Lê Thị
Thu Uyên¹
1Viện Kỹ thuật và Công nghệ, trường Đại học Vinh
Email: hosyphuong@gmail.com; tranphuongnam292003@gmail.com

Abstract
This paper investigates the integration of PID controller, Backstepping controller, and Fuzzy logic for controlling nonholonomic autonomous robots. The main objective is to enhance the robot's mobility and interaction capabilities in real-world environments, focusing on position control for trajectory tracking. The proposed method employs a PID controller to regulate the robot's linear velocity and steering angle. This is combined with a Backstepping controller to address the system's nonlinearities. Additionally, Fuzzy logic is used to adaptively adjust the parameters of the controllers, improving adaptability and robustness under varying conditions. The study emphasizes addressing the overshoot challenge encountered during trajectory tracking. By combining the aforementioned controllers, the proposed method achieves superior performance in maintaining the robot's position along the predefined trajectory while minimizing overshoot within a specified time frame.

Keywords
PID controller, Backstepping controller, Fuzzy logic, Trajectory tracking.

Tóm tắt
Bài báo này tập trung vào nghiên cứu và thực nghiệm
việc kết hợp bộ điều khiển PID, bộ điều khiển Backstepping và Fuzzy logic để kiểm soát robot tự hành dạng noholonomic. Mục tiêu chính của nghiên cứu là cải thiện khả năng di chuyển và tương tác của robot trong môi trường thực tế, đặc biệt là trong việc điều khiển vị trí để bám theo quỹ đạo. Phương pháp này lựa chọn sử dụng bộ điều khiển PID để điều khiển vận tốc tuyến tính và góc lái của robot cùng với bộ điều khiển Backstepping để xử lý các vấn đề phi tuyến tính của hệ thống. Đồng thời, các tham số của bộ điều khiển được điều chỉnh thích ứng bởi Logic mờ. Nghiên cứu nhấn mạnh vào việc đối mặt với thách thức của độ vọt lố khi điều khiển robot bám quỹ đạo. Bằng cách kết hợp các bộ điều khiển trên, nhóm tác giả đã đạt được hiệu suất tốt hơn trong việc duy trì vị trí của robot theo quỹ đạo cho trước, đồng thời giảm thiểu ảnh hưởng của độ vọt lố trong thời gian xác lập.

Ký hiệu
Ký hiệu | Đơn vị | Ý nghĩa
w | rad/s | vận tốc góc
v
θ
| m/s
| rad/s | vận tốc dài
| | hướng của robot
2D 2r | m
| m | khoảng cách giữa tâm hai
| | bánh xe
| | đường kính bánh xe

Chữ viết tắt
PID | Proportional Integral Derivative
WMR | Wheeled Mobile Robots

### 1. Giới thiệu

Hiện nay, robot ngày càng được ứng dụng một cách rộng rãi và phổ biến trong nhiều lĩnh vực khác nhau của cuộc sống. Một khía cạnh quan trọng và không thể thiếu trong kỹ thuật robot có thể đề cập đến ở đây là điều khiển bám quỹ đạo đặt. Nó đề cập đến khả năng đi theo đường dẫn hoặc quỹ đạo cho trước một cách chính xác và hiệu quả, là nền tảng trong các ứng dụng robot khác nhau, bao gồm các phương tiện tự động điều hướng giao thông, máy bay không người lái di chuyển theo đường bay cụ thể hoặc robot di động thực hiện các chuyển động chính xác trong sản xuất. Việc phát triển các thuật toán điều khiển bám quỹ đạo chính xác góp phần nâng cao hiệu suất, độ an toàn và hiệu quả tổng thể của robot. Nhờ một số đặc điểm về tính đơn giản và linh hoạt, robot di động có bánh xe cũng được ứng dụng nhiều trong các công việc nguy hiểm hoặc ở các vị trí không thuận lợi, vì vậy việc nghiên cứu nâng cao chất lượng điều khiển robot dạng ngày vẫn luôn nhận được sự quan tâm của các nhà khoa học. Điều khiển robot bám quỹ đạo trên cơ sở động học và động lực học cũng được đề cập trong nhiều nghiên cứu [[1]-[4]], tuy nhiên trước các thách thức về vấn đề phi tuyến và nhiễu loạn trong môi trường thực nghiệm thì như vậy là chưa đủ. Để đối phó với các vấn đề này, cũng đã có nhiều công bố được đưa ra với các cách tiếp cận khác nhau. Điều khiển trượt là một trong những lựa chọn được đưa ra trong [5]-7], tuy nhiên hiện tượng chattering lại là một thách thức lớn khi đối diện với các nhiễu lớn hơn. Điều khiển thích nghi trên cơ sở ứng dụng Neural network, một sơ đồ điều khiển đã được đề xuất để giải quyết vấn đề điều khiển bám quỹ đạo trong điều kiện tham số mô hình là thay đổi trong quá trình chuyển động [8]. Tuy nhiên, việc xử lý đáp ứng thời gian thực trong thực nghiệm là bất khả thi vì tính phức tạp của phương pháp. Một hướng tiếp cận khá đơn giản và hiệu quả phải kể đến là bộ điều khiển Backstepping [9-12], với những ưu điểm trong cải thiện hiệu suất và độ bền của hệ thống [13].
Trong nghiên cứu này, tác giả đề xuất một bộ điều khiển bám quỹ đạo cho mô hình robot thực nghiệm, trên cơ sở kết hợp sự đơn giản trong cấu trúc của bộ điều khiển Backstepping, tính thực tế của bộ điều khiển PID và kinh nghiệm điều khiển trong Logic mờ nhằm tối ưu hóa khả năng điều khiển bám quỹ đạo và chống lại ảnh hưởng từ các nhiễu không mong muốn từ môi trường phía ngoài cũng như sự thay đổi của tham số mô hình robot trong quá trình hoạt động. Từ đó nâng cao hiệu suất và đảm bảo sự ổn định cho hoạt động của robot.
Cấu trúc của bài báo bao gồm 5 phần, trong đó phần 2 phân tích và mô hình hóa robot di động. Phần 3 thiết kế bộ điều khiển bám quỹ đạo cho robot được đề xuất trên cơ sở kết hợp các bộ điều khiển Backstepping, PID và Fuzzy. Phần 4 thể hiện kết quả thực nghiệm và hiệu quả của bộ điều khiển trên mô hình thực tế. Cuối cùng là nhận xét và kết luận ở phần 5.

### 2. Mô hình hoá robot

### 2.1 Mô hình toán học

Cấu trúc của robot di động được thiết kế có bốn bánh xe. Hai bánh xe ở giữa là 2 bánh chủ động, được điều khiển bởi hai động cơ DC. Một bánh xe phía trước và sau thân robot là 2 bánh thụ động.
Cấu trúc robot được thể hiện trong H. 1. Điểm G là trọng tâm robot, 2 động cơ được sắp xếp đồng trục.


H. 1 Cấu trúc robot di động

Hệ toạ độ tại điểm G{ORXRYR} gắn trên thân robot được gọi là hệ toạ độ robot hoặc hệ toạ cục bộ vì hệ toạ độ này được dịch chuyển theo chuyển động của robot di động. Hệ toạ độ còn lại {OXY} được gọi là hệ toạ độ quán tính hay hệ toạ độ cố định, được sử dụng khi làm việc trên vị trí của robot. Hai hệ toạ độ này lần lượt được biểu diễn như sau:

T
R | r | r | r
| | T
q | | | | | x y
q | | | | | x y | | | (1)

Một ma trận biến đổi Rot(θ) được sử dụng để chuyển đổi giữa hệ toạ độ cố định và hệ toạ độ robot:

1
( ) | ( ) R | R q | Rot | q | q | Rot | q | (2)

Trong đó:

1

| cos | sin | 0
( ) | sin | cos | 0
| 0 | 0 | 1
Rot | (3)

### 2.2 Mô hình động học

Động học của robot liên quan đến mối quan hệ giữa vị trí, vận tốc, gia tốc và các cấu trúc vật lý của nó. Bằng cách thay đổi vận tốc của hai bánh xe, quỹ đạo của
robot có thể thay đổi . | , R | L

lần lượt là vận tốc quay

của bên phải và bên trái. Ta có:

R | R
L | L
V | r
V | r

(4)

VR
và

VL

là vận tốc tuyến tính bánh xe phải và trái. Với bất ký trường hợp nào, v

và có thể được tính
như sau:
( | )
2
R | L
V | V
v
(5)

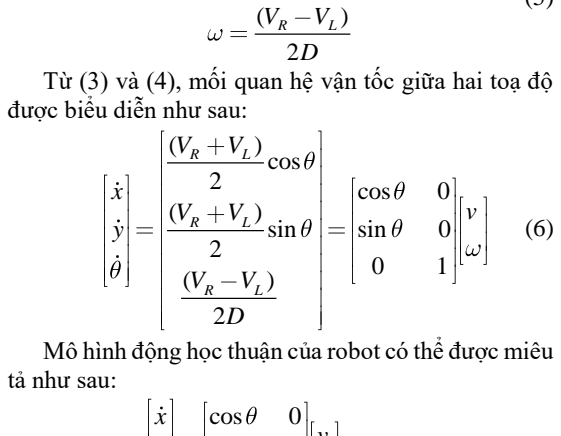
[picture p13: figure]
được biểu diễn như sau:; cos; ) sin; sin; tả như sau:

Từ (3) và (4), mối quan hệ vận tốc giữa hai toạ độ

Mô hình động học thuận của robot có thể được miêu

sin | 0 | ( ) ( )
0 | 1

v
y | S q V t | (7)

### 2.3 Mô hình động lực học

Phân tích động lực học của robot có thể được định nghĩa là kiểm tra mối quan hệ giữa độ lớn mô-men xoắn hoặc độ lớn lực tác dụng lên bánh xe bởi bộ truyền động, vị trí, vận tốc và gia tốc của robot theo thời gian. Sự khác biệt giữa mô hình động lực học và mô hình động học là mô hình động học chỉ xem xét chuyển động với các quan hệ hình học chi phối hệ thống mà không xem xét các lực tác động đến chuyển động.
Theo [14], mô hình động lực học tính được như sau:

( ) | ( , ) | ( ) | ( )
( ) | ( )
M q q V q q q | F q | G q | d
| B q | A q

(8)

q, q˙ và q¨ lần lượt chỉ định các vectơ vị trí, vận tốc và gia tốc tương ứng. M(q) là ma trận quán tính xác định dương đối xứng, V(q, q˙ ) là ma trận hướng tâm và Coriolis, G(q) là lực hấp dẫn vectơ, τd biểu thị các nhiễu hoặc nhiễu không xác định giới hạn, bao gồm cả động lực học phi cấu trúc không được mô hình hóa, B(q) là ma trận biến đổi đầu vào, τ là vectơ mô-men xoắn đầu vào, A

| | τ
(q) là ma trận được liên kết với các ràng buộc và λ là vectơ của các lực ràng buộc. Bỏ qua lực hấp dẫn G(q), ma sát của bánh xe được truyền vào hệ có sai số được xác định trong mô hình động học nên Fq()

bị bỏ qua, giá trị nhiễu được cộng vào tín hiệu điều khiển của cơ cấu chấp hành nên ta bỏ qua trong mô hình động. m

là khối lượng và
I

biểu thị mô men
quán tính của robot, ta có:
| | 00
( ) | 0 | 0 , ( ) | 0, ( ) | 0
0 | 0

m
M q | m | G q | F q
I

1

2

| cos | cos
1
Bq( ) | sin | sin ,
r
| D | D

1

2

3

| 0 | | sin
( , ) | 0 , | ( ) | cos
| 0 | | 0
T V q q | A q | (9)

Phương trình động lực học của robot được viết lại như sau:

M q q | B q | A q ( ) | ( ) | ( ) | (10)

Ma trận S(q) được sử dụng để rút gọn. Ma trận S(q) là ma trận động học tịnh tiến được sửa đổi liên quan đến khoảng cách giữa trọng tâm của robot và trục bánh xe, như đã thấy trong phương trình động học tịnh tiến:

q | S q() | (11)
Ma trận gia tốc thu được bằng cách lấy đạo hàm thời gian phương trình (11) như sau:
q | S q | S q ( ) | ( ) | (12)
Sử dụng phương trình (10) và (12), mô hình robot được sửa như sau:
M q S q | M q S q | B q | A q ( ) ( ) | ( ) ( ) | ( ) | ( ) | (13)
Nhân cả 2 vế cho ma trận biến đổi S

T
(q), ta có:
( ) ( ) ( ) | ( ) ( ) ( )
( ) ( ) | ( ) | ( )
T | T
T | T
S q M q S q | S q M q S q
S q B q | S q A q

(14)

Với S

T
(q)A

T
(q) = 0, phương trình (14) được viết lại dưới dạng:
M q | V q q | B q ( ) | ( , ) | ( ) | (15)

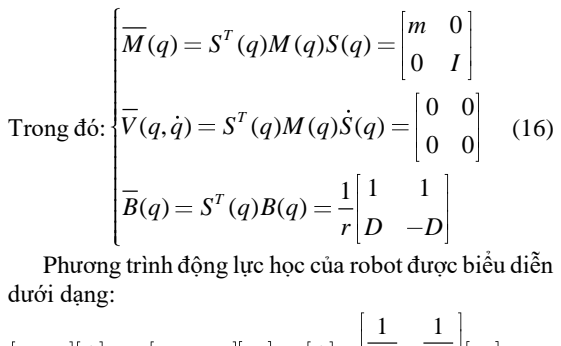
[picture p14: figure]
Trong đó:; dưới dạng:

Phương trình động lực học của robot được biểu diễn

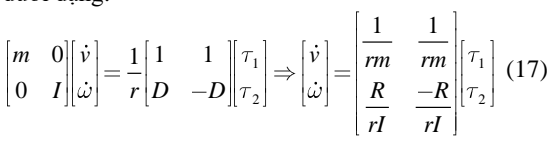
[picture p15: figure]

### 3. Thiết kế bộ điều khiển

Cấu trúc bộ điều khiển được đề xuất ở đây bao gồm 2 vòng điều khiển. Vòng lặp ngoài được thiết kế trên cơ sở động học của robot (kinematic controller) nhằm bám quỹ đạo đặt, bộ điều khiển này là sự kết hợp của bộ điều khiển Backstepping với khả năng chống lại các nhiễu tác động từ môi trường hoặc từ mô hình robot bằng Logic mờ để tự chỉnh định các tham số trong bộ điều khiển. Vòng lặp trong sử dụng bộ điều khiển PID để đảm bảo cho vận tốc dài và vận tốc góc của robot bám với giá trị điều khiển mong muốn. Cấu trúc của bộ điều khiển được thể hiện trên H. 2.

Backsteping Controller

qd =

x
y
θ

d

d

d

Vc =

vc ωc

Outer loop | Fuzzy

logic

| kx ky kth

PID
Controller

Transformation Matrix

uRuL | Driver, Motor R,L

| Sensor Block

vR
vL

vR
vL

c

c

Dynamic Model
Transformation
Invmatrix

vω

Inner loop

H. 2 Cấu trúc bộ điều khiển đề xuất

### 3.1 Bộ điều khiển Backstepping

Với

T
q x y

và

T
R | r | r | r q | x y

lần lượt là vị trí
trong hệ toạ độ cố định và hệ toạ độ robot. Sự khác biệt giữa

q
và

R q

cho các giá trị sai lệch về vị trí của robot trong hệ tọa độ chuẩn. Phương trình sai lệch bám vị trí của robot được chỉ ra Error! Reference source not found.:
cos | sin | 0
sin | cos | 0
0 | 0 | 1
| e | r
q | e | r
| e | r
| x | x | x
e | y | y | y | (18)

Đạo hàm cả 2 vế ta có:

cos
sin
e | e | r | e
q | e | e | r | e

r e

x | y | v v
e | y | x | v | (36)

Dựa trên cách tiếp cận được phát triển trongError! Reference source not found., luật điều khiển động học được áp dụng như sau:
| | cos
( | sin )
c | r | e | x e
c | r | r | y e | e
v | v | K x
| v K y | K

(37)

Kx,Ky và Kθ là các giá trị dương. Thông thường, để thiết kế các tham số này đòi hỏi quá trình nhận dạng hệ thống với các thuật toán phức tạp. Ở đây nhóm tác giả đề xuất một bộ điều khiển mờ dựa trên cơ sở sai lệch vị trí của robot trong thực tế. Bộ điều khiển này có khả năng điều chỉnh tự động các tham số này một cách hiệu quả.

### 3.2 Logic mờ

Bộ điều khiển mờ dựa trên kinh nghiệm, dùng các luật ngôn ngữ IF- THEN để điều khiển đặc tính của robot. Ưu điểm của phương pháp này là tín hiệu điều khiển trơn. Đầu vào của bộ mờ hóa là các biến sai số vị trí và góc của robot di động so với quỹ đạo thiết kế, sau bộ giải mờ là vận tốc góc của bánh trái và vận tốc bánh phải robot. Các biến đầu vào/ ra sử dụng hàm tam giác để giảm thời gian tính toán mà vẫn đạt được độ chính xác cần thiết. Các luật hợp thành là phần khó nhất trong quá trình thiết kế, dựa trên kinh nghiệm về điều khiển và mô phỏng robot.

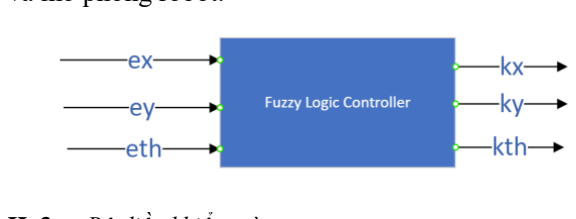
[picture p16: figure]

H. 3 Bộ điều khiển mờ

Các hàm thành viên tương ứng với đầu vào và xuất ra các tập mờ e, e’ và K có trong H. 3.

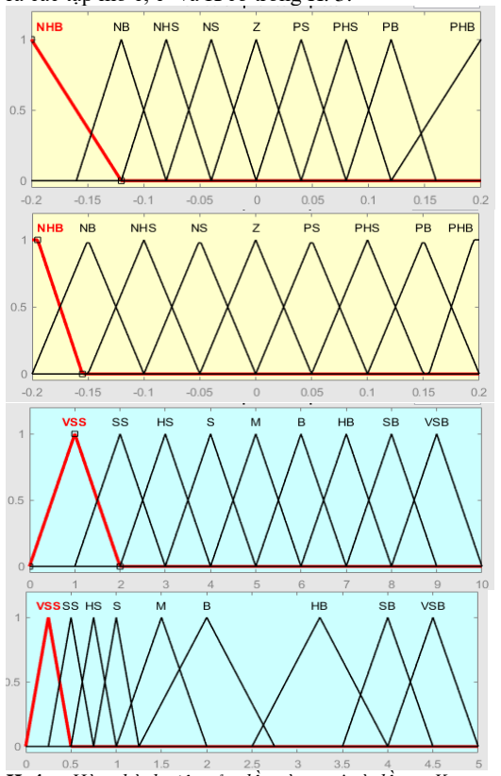
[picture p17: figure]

H. 4 Hàm thành viên của đầu vào e, e’ và đầu ra K

Đầu vào của các biến điều khiển luật 9 biến bao gồm: NHB (Negative High Big), NB (Negative Big), NHS (Negative High Small), NS (Negative Small), Z (Zero), PS (Positive Small), PHS (Positive High Small), PB (Positive Big), PHB (Positive High Big). Đầu ra của luật gồm 9 biến là: VSS (Very Supper Small), SS (Supper Small), HS (High Small), S (Small), M(Middle), B(Big), HB (High Big), S(small), HB (High Big), SB (Supper Big), VSB (Very Supper Big).
Bảng luật mờ được xây dựng:
B. 1 | Luật mờ cho Kx

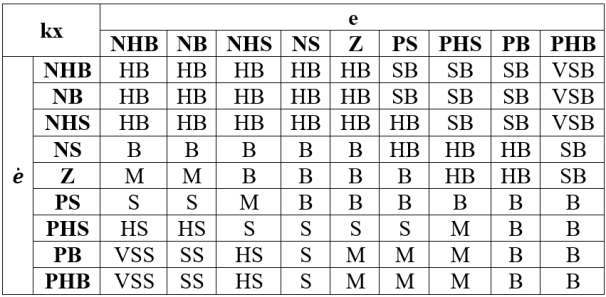
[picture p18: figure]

B. 2 | Luật mờ cho Ky

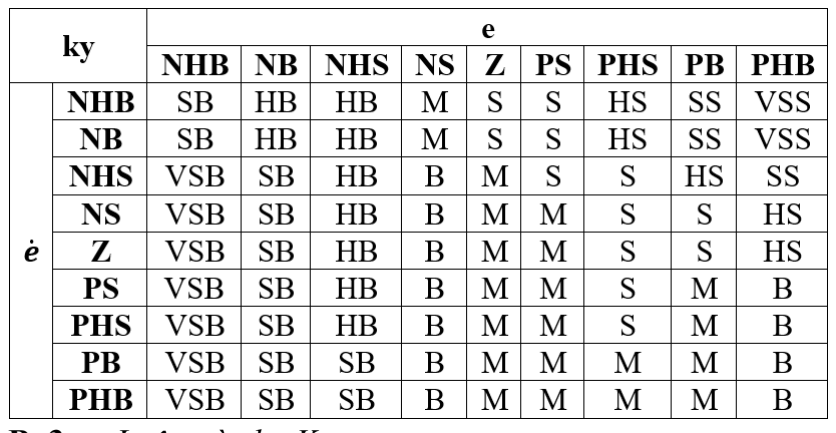
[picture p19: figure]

B. 3 | Luật mờ cho Kth

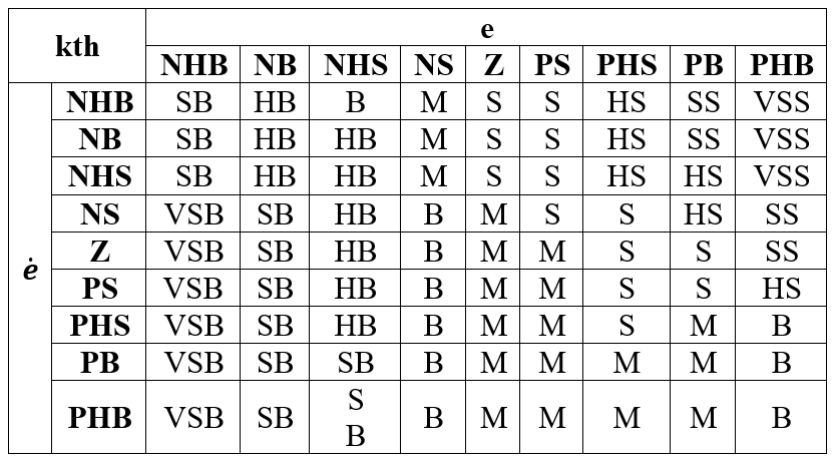
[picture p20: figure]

### 3.3 Bộ điều khiển PID

Phương pháp điều khiển vòng kín thông thường được điều khiển bằng bộ điều khiển PID hay còn gọi là giải thuật PID. PID là tên gọi của bộ điều khiển gồm 3 thành phần Proportional (P) là tỉ lệ, Integral (I) là tích phân và Derivative (D) là vi phân. Bộ điều khiển PID hiệu chỉnh sai số giữa giá trị đo được và giá trị mong muốn bằng cách tính toán ra một tín hiệu điều khiển để giữ cho sai lệch ở mức nhỏ nhất có thể được. Bộ điều khiển này có 3 tham số Kp, Kivà Kd để điều chỉnh sai số của bộ điều khiển.

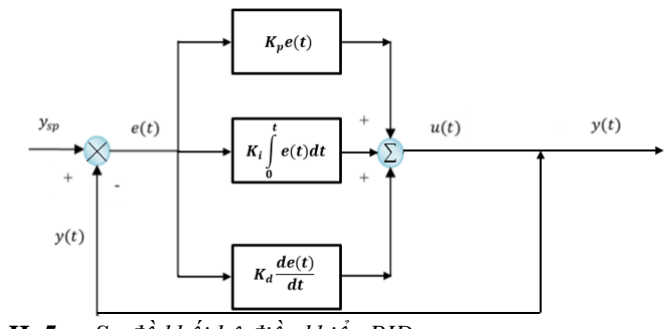
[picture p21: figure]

H. 5 Sơ đồ khối bộ điều khiển PID

Phương trình bộ điều khiển PID được sử dụng:

0

( ) | ( ) | | ( ) ( )

t

p | d i

de t
u t | K e t | K | e t d t | K
dt
Sai lệch e(t) tại thời điểm t: độ lệch giữa giá trị mong muốn và giá trị đo được.
( ) | sp e t | y t | y
Trong đó:
+

sp y

: giá trị mong muốn.

+

yt

: giá trị đo được tại thời điểm t. Theo H. 2 bộ điều khiển PID được sử dụng để điều chỉnh cho vận tốc tuyến tính và vận tốc góc của robot bám với giá trị mong muốn dựa vào độ sai lệch. Từ đó điều khiển 2 động cơ gắn với 2 bánh chủ động của robot. Độ sai lệch được tính toán trong bộ điều khiển PID là độ lệch giữa vận tốc đặt với vận tốc thực tế. Có nhiều phương pháp xác định tham số của bộ điều khiển PID [15],[16], trong bài báo này nhóm tác giả sử dụng phương pháp Ziegler-Nichols thứ 2.
Các bước xác định thông số PID cho hệ thống theo phương pháp Ziegler–Nichols thứ 2:
+ Đầu tiên đặt Ki = 0 và Kd = 0.
+ Chỉ sử dụng tác động khuếch đại, tăng Kp từ 0 tới một giá trị tới hạn Kcr, tại đó đầu ra của hệ thống có dạng dao động điều hoà.
+ Xác định Kp và chu kỳ dao động Pcr bằng thực nghiệm.

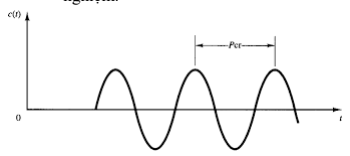
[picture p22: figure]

H. 6 Chu kỳ dao động Pcr

Xác định các tham số Kp, Kivà Kd của bộ điều khiển theo bảng sau:
B. 4 | Phương pháp Ziegler–Nichols
Type of Controller | Kp | Ki | Kd
P | 0.5Kcr | 0 | 0
PI | 0.45Kcr | 0.85Pcr | 0
PID | 0.6Kcr | 0.5Pcr | 0.125Pcr
Tính toán Kivà Kd của hệ thống dựa vào Pcr từ đó tìm được tham số của bộ điều khiển PID. Sau quá trình thực nghiệm, các giá trị của bộ điều khiển tìm được như sau:
0.02, | 0.00015 K | K p | i
và
0.01. Kd

### 4. Kết quả thực nghiệm

Trong phần này, kết quả thực nghiệm được trình bày để kiểm tra tính hiệu quả và độ chính xác của việc kết hợp các bộ điều khiển.
Các thông số thực nghiệm được xác định trong B. 5.
B. 5 | Thông số thực nghiệm
Thông số Robot | L = 0.37m, r = 0.1m
Thông số bộ PID | Kp = 0.002, Ki = 0.00015, Kd = 0.01

Vị trí ban đầu của robot được đặt tại tọa độ (0, 0, 0); Quỹ đạo đặt là hình tròn được biểu diễn bởi phương trình:
cos( )
sin( )

d

d

x | R | t
y | R | t
Với bán kính quỹ đạo R = 150 cm và ω = 0.2 rad/s

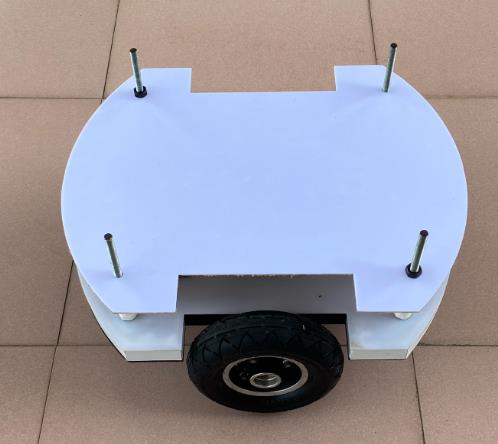
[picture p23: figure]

H. 7 Mô hình robot thực nghiệm

Link video thực nghiệm:
https://www.youtube.com/watch?v=6Xz11GfAjuo

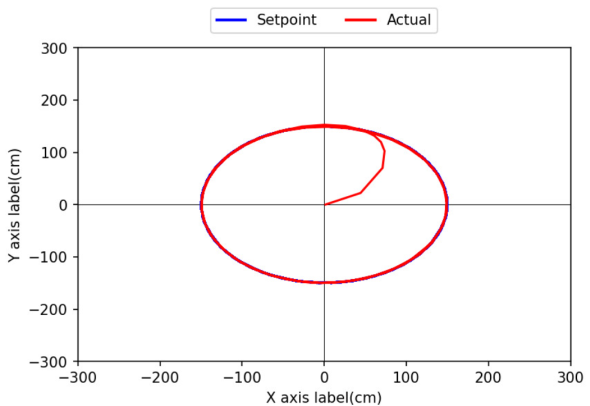
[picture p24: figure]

H. 8 | Quỹ đạo chuyển động thực tế của robot


H. 9 | Sai lệch theo trục x, y và góc lái theta


H. 10 Đồ thị sai lệch ex = xd − x


H. 11 Đồ thị sai lệch ey = yd − y


H. 12 Đồ thị sai lệch góc lái: etheta = tℎetad − tℎeta


H. 13 Tín hiệu điều khiển

Sai lệch theo các trục x,y và góc lái theta thể hiện trên hình H. 9, H. 10,H. 11, H. 12 cho thấy robot đã bám theo quỹ đạo đặt với khoảng sai số chấp nhận được với tín hiệu điều khiển là vận tốc dài và vận tốc góc đạt được sau khối kinematic control.
Trong thực tế, khi chịu tác động bới ngoại lực làm lệch quỹ đạo chuyển động của robot (link video), bộ điều khiển đề xuất đã nhanh chóng giúp robot bám lại quỹ đạo đặt ban đầu.

### 5. Kết luận

Bằng cách kết hợp các bộ điều khiển như PID, Backstepping và Fuzzy logic vào ứng dụng thực nghiệm đã chứng minh rằng bộ điều khiển đề xuất hoạt động ổn định và đáng tin cậy trong bài toán điều khiển bám theo quỹ đạo đặt. Bộ điều khiển logic mờ đã giúp cải thiện khả năng thích ứng của hệ thống với biến động của môi trường. Tuy nhiên, nhận thức rõ ràng về tiềm năng của nghiên cứu, nhóm đề xuất hướng phát triển tiếp theo có thể thực nghiệm thêm thêm một số bộ điều khiển khác để kiểm chứng, so sánh tính hiệu quả, sự ổn định của hệ thống.

### 6. Cảm ơn

Bài báo được tài trợ bởi Đề tài cấp Viện Hàn lâm KHCN Việt Nam “Nghiên cứu, hoàn thiện thiết kế và chế tạo mẫu robot dạng người thông minh IVASTBot ứng dụng trong giao tiếp lễ tân văn phòng”, mã số CT0000.01/24-25.

Tài liệu tham khảo

[1] J. V. Steen, M. Reyhanoglu, "Trajectory Tracking Control of a Rolling Disk on a Smooth Manifold", The 12th Asian Control Conference (ASCC) Kitakyusyu International Conference Center, Japan, 43-48, 2019.
[2] D. Ben Halima Abid, N. Youssfi Allagui, and N, Derbel, Navigation and trajectory tracking of mobile robot based on kinematic PI controller, The 17th international conference on Sciences and Techniques of Automatic control and computer engineering (STA'17), Monastir, Tunisia, 2017.
[3] T. Obeidi, C. Larbes, A. Ilinca, G. Filiz, and T. Kebir, "Fuzzy logic based maximum power point tracking for a solar electric vehicle", Acta polytechnica hungaria, 15(7), 133-156, 2018.
[4] S. Sahloul, D. Ben Halima, C. Rekik, "Comparative study of hybrid Fuzzy logic methods for mobile robot navigation in unknown environments", The 19th International Conference on Sciences and Techniques of Automatic Control and Computer Engineering (STA'19), Sousse, Tunisia, 170-175, 2019.
[5] I. Hassani, I. Maalej and C. Rekik, "Control points searching algorithm for autonomous mobile robot navigation with obstacle avoidance", The 19th
International | Conference | on | Sciences | and
Techniques of Automatic Control and Computer Engineering (STA'19), Sousse, Tunisia, 158-163, 2019.
[6] I. Hassani, I. Maalej and C. Rekik, “Robot path planning with avoiding obstacles using free
segments | and | turning points | algorithms”,
Mathematical problem in Engineering, 2018(6), 1-13, 2018.
[7] H. S. Phuong, N. M. Tien, N. D. Tan, M. T. Anh and D. D. Tu, "Proposal of a Fault-tolerant controller for wheeled mobile robots with faulty actuators," 2023 12th International Conference on

Control, Automation and Information Sciences (ICCAIS), Hanoi, Vietnam, 2023, pp. 507-512
[8] Zhang, L., Liu, L., & Zhang, S. (2020). Design, implementation, and validation of robust fractional-order PD controller for wheeled mobile robot
trajectory | tracking. | Complexity, | Hindawi,
Complexity, 2020(4), 1-12.
[9] Y. Koubaa, M. Boukattaya, and T. Damak, "Intelligent control for nonholonomic mobile robot
including | actuator | dynamics," | International
Multiconference on Systems, Signals, and Devices (SSD18), Hammamet, Tunisia, 1012-1016, 2018.
[10] A. Mino, K. Uchiyama and K. Masuda, "Backstepping Control for Satellite Attitude Control Using Spherical Control Moment Gyro", 2019 SICE International Symposium on Control Systems(SICEISCS),Japan,DOI:10.23919/SICEIS CS.2019.8758769.
[11] W. G. Wu, H. T. Chen, and Y. J. Wang, "Global trajectory tracking control of mobile robots" Acta Automatica Sinica, vol. 27, pp. 326-331, 2001.
[12] G. Zidani, S. Drid, L. Chrifi-Alaoui, A. Benmakhlouf, and S. Chaouch, "Backstepping controller for a wheeled mobile robot" in Proc. 2015 4th International Conference on Systems and Control (ICSC), 2015, pp. 443-448
[13] Y. Huang, L. Chong, Z. Li, W. Gao, H. Lu, L. Wei, Backstepping sliding mode control for robot manipulator via nonlinear disturbance observer, Proceedings of the 38th Chinese Control Conference, Guangzhou, China, 3220-3224, 2019.
[14] Mustafa Ayyıldız & Umut Tilki (2023) Adaptive sliding mode based fault tolerant control of wheeled
mobile | robots, Automatika, 64:3, 467-
483, DOI: 10.1080/00051144.2023.2190866 (https://doi.org/10.1080/00051144.2023.2190866)
[15] Huang, M., Tian, M., Liu, Y. et al, “Parameter optimization of PID controller for water and fertilizer control system based on partial attraction
adaptive | firefly | algorithm”, | Sci | Rep
12,12182(2022). | https://doi.org/10.1038/s41598-
022-16425-7.
[16] Hekimoglu, B, “Optimal tuning of fractional order PID controller for DC motor speed control via chaotic atom search optimization algorithm”, IEEE Access 7, 38100–38114 (2019).

Hồ Sỹ Phương, sinh năm 1986, nhận bằng Thạc sĩ chuyên ngành Kỹ thuật điều khiển và Tự động hóa của Học viện Kỹ thuật quân sự năm 2013. Hiện tại là giảng viên Viện Kỹ thuật và Công nghệ, Trường ĐH Vinh. Từ năm 2023 là nghiên cứu sinh tại Viện Hàn lâm khoa học và công nghệ Việt Nam, hướng nghiên cứu chính: Robotics, điều khiển thích nghi, điều khiển mờ và mạng nơ ron.

Trần Phương Nam, sinh năm
2003, sinh viên ngành Kỹ thuật Điều khiển và tự động hóa, viện Kỹ thuật và Công nghệ, trường Đại học Vinh. Hướng nghiên cứu: Robotic, điều khiển thích nghi, mạng nơ ron.

Mai Thế Anh, sinh năm 1987, nhận bằng Tiến sĩ chuyên ngành Điều khiển học kỹ thuật và lí thuyết thông tin của Trường ĐH năng lượng Moscow năm 2018. Hiện tại là giảng viên Viện Kỹ thuật và Công nghệ, Trường Đại học Vinh. Hướng nghiên cứu chính: robotics, mạng neural, điều khiển mờ, mô hình hóa và mô phỏng hệ thống điều khiển tự động.

Lê Văn Chương, sinh năm 1985, bảo vệ luận án Tiến sĩ chuyên ngành Kỹ thuật điều khiển và Tự động hóa tại Viện Khoa học và công nghệ quân sự năm 2023. Hiện tại là giảng viên Viện Kỹ thuật và Công nghệ, trường Đại học Vinh. Hướng nghiên cứu chính: các phương pháp phân tích và tổng hợp các hệ thống điều khiển tự động.

Dương Đình Tú, sinh năm 1986, nhận bằng Tiến sĩ chuyên ngành Điều khiển học kỹ thuật và lí thuyết thông tin của Trường ĐH giao thông Moscow năm 2018. Hiện tại là giảng viên Viện Kỹ thuật và Công nghệ, Trường Đại học Vinh. Hướng nghiên cứu chính: thị giác máy tính trong kỹ thuật điều khiển, robotics, neural networks.

Lê Thị Thu Uyên, sinh năm 2003, sinh viên ngành Kỹ thuật Điều khiển và tự động hóa, viện Kỹ thuật và Công nghệ, trường Đại học Vinh. Hướng nghiên cứu: Robotic, điều khiển thích nghi.

Phan Văn Vỹ, sinh năm 2003, sinh viên ngành Kỹ thuật Điều khiển và tự động hóa, viện Kỹ thuật và Công nghệ, trường Đại học Vinh. Hướng nghiên cứu: Robotic, điều khiển logic mờ.

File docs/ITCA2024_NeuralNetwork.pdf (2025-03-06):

# Kiểm chứng thực nghiệm bộ điều khiển thích nghi mạng nơ-ron cho robot di động bám quỹ đạo

Hồ Sỹ Phương¹,2*
, Dương Đình Tú¹

, Trần Phương Nam¹
, Nguyễn Thành Trí¹
, Lê Thị Thu Uyên¹
, Đặng
Thái Sơn¹
, Phan Văn Vỹ

1
1Viện Kỹ thuật và Công nghệ, Trường Đại học Vinh,

2Học viện Khoa học và Công nghệ, Viện Hàn lâm Khoa học và Công nghệ Việt Nam
Email: hophuong@vinhuni.edu.vn, tranphuongnam292003@gmail.com

Abstract— Trong bài báo này, chúng tôi đề xuất một mô hình điều khiển thích nghi cho robot di động hai bánh vi sai (WMR) dựa trên mạng nơ-ron để bám quỹ đạo. Đóng góp chính của nghiên cứu nằm ở việc kiểm chứng bộ điều khiển trực tiếp trên mô hình robot thực tế thay vì chỉ dựa vào mô phỏng. Bộ điều khiển sử dụng mạng nơ-ron có khả năng tự động học hỏi từ dữ liệu thời gian thực và điều chỉnh theo sự thay đổi của môi trường, nhờ đó cải thiện hiệu suất điều khiển và giảm sự phụ thuộc vào các mô hình động lực học phức tạp. Kết quả cho thấy bộ điều khiển dựa trên mạng nơ-ron đạt độ chính xác cao trong việc bám quỹ đạo trong môi trường thực nghiệm với hiểu biết về động lực học là hạn chế. Bài báo cũng trình bày chi tiết quá trình thiết kế, triển khai và các kết quả thực nghiệm để chứng minh tính hiệu quả và độ tin cậy của phương pháp.

Keywords- Robot di động có bánh xe, điều khiển thích nghi, mạng nơ-ron, bám quỹ đạo, học thời gian thực.

I. GIỚI THIỆU

Robot di động 2 bánh vi sai (DDMR) được sử dụng rất phổ biến trong các ứng dụng công nghiệp và dịch vụ. Tuy nhiên, việc điều khiển chính xác quỹ đạo của robot trong môi trường thực tế gặp nhiều thách thức do sự xuất hiện của nhiễu và các yếu tố môi trường thay đổi liên tục [1][2]. Các phương pháp điều khiển truyền thống như PID hoặc điều khiển trượt (SMC) được áp dụng rộng rãi, nhưng chúng phụ thuộc nhiều vào các mô hình động lực học chính xác của hệ thống, làm cho việc đối phó với các nhiễu động và biến đổi không dự đoán trước trở nên khó khăn [3][4].
Để khắc phục những hạn chế này, mạng nơ-ron nhân tạo (ANN) đã được sử dụng trong các bộ điều khiển để học và thích nghi với môi trường thay đổi, cải thiện khả năng bám quỹ đạo của robot mà không cần dựa vào các mô hình động lực học phức tạp [5]. Các nghiên cứu trước đây đã cho thấy mạng nơ-ron có khả năng ước lượng các tham số hệ thống và xử lý tốt các yếu tố bất định trong môi trường hoạt động của robot [6][7]. Tuy nhiên, nhiều nghiên cứu chỉ tập trung vào mô phỏng mà chưa thử nghiệm trực tiếp trên các hệ thống thực tế [8].
Trong nghiên cứu này, chúng tôi thực hiện kiểm chứng một bộ điều khiển thích nghi dựa trên mạng nơ-ron cho robot di động. Bộ điều khiển này không chỉ bám quỹ đạo chính xác trong môi trường có nhiễu và các yếu tố biến đổi mà còn cải thiện độ ổn định và giảm thiểu sai số [9]. Bộ điều khiển được thiết kế với khả năng tự học và điều chỉnh các tham số động lực học chưa biết thông qua mạng nơ-ron, giúp tối ưu hóa quá trình điều khiển và giảm phụ thuộc vào các mô hình toán học [10].
Kết quả thử nghiệm cho thấy bộ điều khiển thích nghi này đạt được hiệu suất cao trong bám quỹ đạo và đảm bảo tính ổn định của hệ thống ngay cả trong môi trường thực tế có nhiễu động lớn [11]. Nghiên cứu này không chỉ cung cấp một giải pháp điều khiển hiệu quả cho robot di động mà còn mở ra tiềm năng ứng dụng trong các hệ thống điều khiển tự động khác.
Nội dung nghiên cứu gồm 5 phần, phần 2 giới thiệu về mô hình hóa robot và bản thiết kế phần cứng của robot. Phần 3 trình bày bộ điều khiển đề xuất với khả năng tự chỉnh định các tham số điều khiển nhờ sử dụng mạng nơ ron. Phần 4 trình bày các kết quả đạt được khi áp dụng thuật toán trên mô hình thực nghiệm, cuối cùng là kết luận thể hiện trong phần 5.

II. MÔ HÌNH ROBOT
Mô hình được nghiên cứu, thiết kế và chế tạo ở đây có cấu trúc cơ bản thể hiện trên hình 1. Robot chuyển động phụ thuộc hoàn toàn vào bộ truyền động của 2 bánh xe bán kính r gắn trên 2 động cơ DC servo được bố trí đồng trục. Vận tốc góc và vận tốc dài tương ứng của bánh phải và bánh trái được ký hiệu lần lượt là
, | ( | , ) i | i ω v i R L = | . | [ | ]

T
ζ ω = v

là véc tơ thể hiện vận tốc

dài của robot. bánh thụ động phía trước sau giữ vai trò thăng bằng cho robot. Bề rộng của robot là 2h, trọng tâm và tâm của robot được thiết kế trùng nhau tại M.
[ | ] ; | [ | ]
T | T
q | x | y | q | x | y = | =
M | M | M | d | d | d | d α | α

là vị trí tương
ứng của robot trong 2 hệ tọa độ (hệ tọa độ toàn cục và di động được thể hiện tương ứng trên hình 1).

vL

2h

M

XR

YR

vR

Y

O | xM | X

yM

v

ω
α

2r

Hình 1. Cấu trúc và hệ toạ độ của robot
Vị trí tương ứng của robot trong hai hệ tọa độ bao gồm:
[ | ] ; | [ | ]
T | T
M | M | M | d | d | d | d q | x | y | q | x | y = | = α | α
Mối quan hệ giữa vận tốc của robot trong hai hệ tọa độ được thể hiện thông qua phương trình:
cos | sin | 0
sin | cos | 0
0 | 0 | 1
| M | d
d | M | d
| M | d
| | x | x
q | Sq | y | y
α | α
α | α
| | α | α
é | ù é | ù é ù -
ê | ú ê | ú ê ú = | Û | = ê | ú ê | ú ê ú ê | ú ê | ú ê ú ë | û ë | û ë û
(1)

Động học của robot liên quan đến mối quan hệ giữa vị trí, vận tốc, gia tốc và các cấu trúc vật lý của nó.
Vận tốc dài của mỗi bánh xe:
R | R
L | L
v | r
v | r ω
| ω

ì =
í
î =

(2)

Thành phần vận tốc của robot:

( | )
2 | 2
( | )
2 | 2
R | L
R | L
R | L
R | L
v | v | r
v
v | v | r
h | h
ω | ω
ω | ω | ω
ì | +
= | = | + ïï
í
- ï = | = | - ïî

(3)

Với giả thiết robot di động không có trượt ngang và trượt dọc, 2 bánh vi sai luôn tiếp xúc với mặt đất. Vận tốc tại điểm “M” sẽ được tính như sau:

1 | 1
0 | 0
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
é | ù éù | ê | ú êú | éù
= ê | ú êú | êú ê | úëû êú ëû | ê | ú -
ë | û

(4)

Kết hợp (1), (3) và (4), phương trình động học của robot được biểu diễn như sau:

q H= ζ

(5)
Trong đó:
cos | 0
sin | 0 ;
0 | 1

v
H

α
α ζ
ω
é | ù
ê | ú | éù
= | = ê | ú | êú ëû ê | ú ë | û
III. | THIẾT KẾ BỘ ĐIỀU KHIỂN THÍCH NGHI TRÊN CƠ SỞ MẠNG NƠ RON

Phương pháp điều khiển theo quỹ đạo thường được áp dụng trong các môi trường đã biết và dựa trên động học của robot. Tuy nhiên, khi các yếu tố động lực như quán tính, khối lượng hay vị trí khối lượng thay đổi, cần phải xem xét đến động lực học của robot. Mục tiêu chính là giúp robot bám sát quỹ đạo đề ra, nhưng sự phức tạp của hệ thống cùng các yếu tố bất định, nhiễu loạn hay lỗi cảm biến có thể gây ra sai lệch trong chuyển động. Để giải quyết những thách thức này, bộ điều khiển được đề xuất có khả năng học hỏi từ động lực học chưa biết, giúp robot bám theo quỹ đạo với độ chính xác cao trong môi trường mô phỏng.
Cấu trúc bộ điều khiển đề xuất được thể hiện trên hình 2 với sự tham gia của bộ điều khiển động học với khả năng thích nghi nhờ sử dụng kiến trúc mạng nơ-ron thể hiện trong hình 3.

Desired Trajectory

Backstepping Controller

Forward Transfor- mation

DC servo motor Right

DC servo motor Left

PID1

PID2

u1

u2

Kinematic Model

vR

vL

vR

Inverse Transfor- mation

vL

Neural Network

k i=(x,y, ) θ
vω

vCωC

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
Hình 2. Sơ đồ cấu trúc bộ điều khiển đề xuất Phương trình sai lệch bám vị trí của robot được chỉ ra trong phương trình (6) [13]:
cos | sin | 0
sin | cos | 0
0 | 0 | 1
| x | d | M
q | y | d | M
| | d | M
| x | x
e | y | y

α

ξ | α | α
ξ | α | α
ξ | α | α
é ù é | ù é | ù -
ê ú ê | ú ê | ú
= | = - | - ê ú ê | ú ê | ú ê ú ê | ú ê | ú ë û ë | û ë | û -

(6)

Đạo hàm cả 2 vế ta có:

cos

sin

x | y | d
y | x | d

d

v | v

v

α

α

α

ξ | ωξ | ξ
ξ | ωξ | ξ
ξ | ω ω
ì = - + | + ïï
í = - | +
ï
ï = - î

(7)

Luật điều khiển động học được đưa ra và áp dụng cho robot được thể hiện qua (8) [12].

1

2 | 3

cos
( | sin | )
c | d | x
c
c | d | d | y
v | v
| v

α

α

| | ξ | λ ξ
ζ
ω | ω | λ ξ | λ | ξ
éù é | ù +
= | = êú ê | ú + | + ëû ë | û

(8)

Trong đó
( 1,2,3) i λ i =

là các giá trị dương. Trong nghiên cứu này chúng được cập nhật một cách liên tục bằng mạng nơ ron giúp robot có khả năng thích ứng tốt hơn trước các nhiễu loạn và các nhân tố ảnh hưởng chưa biết.
Sự điều chỉnh
λi

của bộ điều khiển dựa trên động học để tối thiểu hóa hàm chi phí sau:

1
2

T
L
q q

= ξ γξ

(9)

Trong đó:
1 | 2 | 3 γ | γ γ γ = diag( , , )

là các hệ số của mạng

nơ ron;
λi

là một phần của hàm chi phí và được tối ưu

hóa cũng như cập nhật theo phương pháp gradient descent. Các hệ số này được biểu diễn bởi vector

[ 1 | 2 | 3 ]

T
κ | λ λ λ = | ,
Kết hợp với (6), đạo hàm riêng của hàm chi phí Γ
theo
κ

được tính như sau:

T | T q
q | q

q
T

ξ
ξ γ | ξ γ
κ | κ | κ
∂Γ | ∂ ∂
= | = -
∂ | ∂ | ∂

(10)

Trong đó:
cos | sin | 0
sin | cos | 0
0 | 0 | 1

T

α | α
α | α
é | | | ù
ê | | | ú
=-ê | ú ê | ú ë | û

Áp dụng quy tắc chuỗi, đạo hàm của q theo κ
được khai triển:
11 | 12
21 | 22
31 | 32
0 | 0
0 | sin

x c

c | d y | d
| | J | J
q | q | J | J
v | v
J | J | α
ζ | ξ
κ | ζ | κ | ξ | ξ
é | ù
∂ | ∂ ∂ | é | ù ê | ú
= | = | ê | ú ê | ú ∂ | ∂ | ∂ | ë | û ê | ú ë | û

(11)

Lúc đó, (10) được viết lại như sau:

T
T | T q | c
q | q | TJ
ξ | ζ
ξ γ | ξ γ
κ | κ | κ
∂Γ | ∂ ∂
= | = -
∂ | ∂ | ∂

(12)

Trong đó:

11 | 12
21 | 22
31 | 32
| J | J
J | J | J
| J | J
é | | | ù
ê | | | ú
=
ê | ú ê | ú ë | û


Hình 3. Cấu trúc các lớp của mạng nơ ron Phương pháp tính ma trận Jacobian bằng mạng nơ-ron (NN) được thực hiện bằng cách khởi tạo các trọng số ban đầu cho mô hình, sau đó tinh chỉnh các trọng số này thông qua quá trình huấn luyện. Mạng nơ-ron dự đoán các giá trị thông qua lan truyền xuôi, từ đó xác định sai số bằng cách so sánh giá trị dự đoán với giá trị thực. Sai số này được lan truyền ngược từ lớp đầu ra về lớp đầu vào, sử dụng các đạo hàm để điều chỉnh trọng số, tối ưu hóa mô hình và từ đó tính toán chính xác ma trận Jacobian. Quy trình này đảm bảo mạng nơ-ron có thể học và thích nghi hiệu quả trong các hệ thống điều khiển.
Lớp đầu tiên của mô hình mạng nơ-ron nhận L nơ ron, lớp thứ 2 là m nơ ron.
c ζ

và
xy

ˆˆ
,,α

ˆ

tương ứng là
đầu vào và đầu ra cho mạng nơ-ron. Nh là số nơ ron trong lớp ẩn. Trong khi các giá trị Whi là trọng số từ lớp ẩn tới lớp đầu vào, thì các giá trị Who là trọng số từ lớp đầu ra đến lớp ẩn.
Mối quan hệ giữa các đầu vào
()j

x

và đầu ra
()i

y
của mạng được xác định bởi:

2

0 | 0
1 | 1`

L

i | il | lj j | l | i
l | j
y | Woh | Whi x | v | w σ | σ
= | =
æ | ö æ | ö
= | + | + ç | ÷ ç | ÷ ç | ÷ è | ø è | ø ∑ | ∑
(13)

Hàm kích hoạt được được chọn là hàm sigmoid: 1
1 e

ρ

σ | -

=
+

(14)

Trong đó ρ là biểu diễn của tích giữa trọng số và giá trị neuron dẫn tới lớp mong muốn. Đạo hàm của hàm 2 vế của (14) ta có:

(1 | ( ) f | )

σ
σ ρ
ρ

∂
= -
∂

(15)

Thuật toán lan truyền ngược là một thuật toán điều chỉnh trọng số dựa trên phương pháp giảm dần gradient.
() ( | 1) | ( )
() ( | 1) | ( )
il | il
il
lj | lj
il

Ek W k W k
W
Ek V k V k
V

V

V

ì | ∂
+ | = | - ï
ï | ∂
í
∂ ï | + | = | - ï | ∂ î

(16)

Trong đó
V

là hệ số học (learning rate), nó quyết định bước nhảy trong quá trình giảm thiểu sai lệch (gradient descent). Trọng số được thay đổi theo chu kỳ cho đến khi sai lệch được tối thiểu hóa.
Sai lệch của robot cần tối thiểu hóa được xác định:
( ) | ( ) y ( ) i | i | i e k | Y k | k = | -

(17)
Trong đó
y ( ) i

k

là giá trị đầu ra của mạng nơ-ron

tại bước k, () [ | ]

T
Y k | x | y i | A | A | A
= | α

là vị trí và góc lái của
robot tại một thời điểm A cụ thể, đóng vai trò làm giá trị tham chiếu để so sánh với các giá trị dự đoán của hệ thống.
Bằng cách sử dụng hàm lỗi, hàm chi phí được tìm thấy như sau:

2
() (k)
2

i

k
E

ξ
=

(18)

Các gradient yêu cầu của hàm chi phí E(k) theo trọng số được xác định bằng cách sử dụng quy tắc dây chuyền (chain rule).

( | )

2

1 | 2
( | )
( ) | ( | )
l | i | i
il
j | l | i | i | il
lj

E
z
W
E
x | W
V

σ ρ ξ

σ ρ σ ρ ξ

ì ∂
=- ′
ï
∂ï
í
∂
ï | = - | + ′ | ′ ï∂
î

∑

(19)

Trong đó, zl là đầu ra hàm sigmoid của nơ ron l ở lớp ẩn. Ma trận Jacobian được xác định như sau:

ˆ | ˆ | ˆ | ˆ ( ) | ( | 1) | ( ) | ( | 1)
( ) | ( | 1) | ( ) | ( | 1)
ˆ | ˆ | ˆ | ˆ ( ) | ( | 1) | ( ) | ( | 1)
( ) | ( | 1) | ( ) | ( | 1)
ˆ | ˆ | ˆ | ˆ ( ) | ( | 1) | ( ) | ( | 1)
( ) | ( | 1) | ( ) | ( | 1)
c | c | c | c
c | c | c | c
c | c | c | c
x t | x t | x t | x t
v t | v t | t | t
y t | y t | y t | y t J
v t | v t | t | t
t | t | t | t
v t | v t | t | t
| | ω | ω
| | ω | ω
α | α | α | α
| | ω | ω
é | ù - | - | - | - ê | ú
=
ë | û - | - | - | -

(20)

Thông qua mạng nơ ron, bộ điều khiển động học
(8) thay đổi các giá trị điều chỉnh và thích nghi để làm cho hàm chi phí bằng 0 theo phương pháp giảm dần gradient như sau:
1 | 1 | 1
2 | 2 | 2
3 | 3 | 3
( ) | ( | 1)
( ) | ( | 1)
( ) | ( | 1)
k t | k t | k
k t | k t | k
k t | k t | k
ì | = | - + Δ ï
í | = | - + Δ
ï
î | = | - + Δ

(21)

Trên cơ sở tín hiệu điều khiển động học với khả năng tự điều chỉnh, bộ điều khiển PID được sử dụng để điều khiển hệ truyền động của robot trên cơ sở so lệch sai số vận tốc của robot thực tế với giá trị điều khiển. Cấu trúc bộ điều khiển PID sử dụng có dạng:
u | K | K | dt K m | P | I | D = | + | + ξ | ξ | ξ η | η | η ò
(22)

Trong đó
, | , K K K P | I | D

là các hệ số điều khiển dương tương ứng với các khâu trong bộ điều khiển PID.

IV. KẾT QUẢ VÀ THẢO LUẬN
Trong phần này, chúng tôi thực hiện kiểm chứng bộ điều khiển đề xuất trong môi trường thực nghiệm. Vị trí ban đầu của robot được đặt tại gốc tọa độ (0, 0, 0); Quỹ đạo đặt là hình tròn được biểu diễn bởi phương trình:
sin( )
; | 1.25 , | 0.25rad/ s
cos( )

d

d

x | R | t
R | m
y | R | t ω
ω
| | ω

ì =
í | = | =
î =

(23)

. Tham số của bộ điều khiển PID cho bộ phận truyền động được chọn dựa trên phương pháp thử và sai: Kp = 0.002, Ki = 0.00015, Kd = 0.01. Khoảng cách giữa 2 bánh xe là L=0.38m, bán kính bánh xe: r=0.1m. Bộ điều khiển trung tâm được sử dụng là ESP32, động cơ DC servo được sử dụng ở đây là Planet 24VDC-60W với 13 xung encoder. Mạch XD-160D là mạch lực để điều khiển động cơ DC.


Hình 4. Sơ đồ cấu trúc ghép nối phần cứng
Mô hình thực nghiệm của robot được thể hiện trên hình 5.


Hình 5. Thiết kế và mô hình thực tế của robot
Bộ thông số của mạng nơ ron:
Trọng số từ lớp đầu vào đến lớp ẩn.
Whi = [-6.4855 -4.0100 -4.5498;-6.5890 -4.7984 -2.1504;-6.5339 -3.9266 -4.3257;-7.4260 -3.7515 -2.3720;-6.3217 -4.2807 -3.3511;-6.1753 -4.2071 -3.1082;-8.9702 -5.8552 -4.7596;-7.3099 -6.6322 -4.5009;-6.2155 -5.9031 -5.4120;-5.9862 -3.5501 -3.1355;-5.9129 -4.1946 -3.8804;-6.3110 -4.0644 -2.8849;-6.2365 -2.9500 -2.3163;-8.2328 -6.5682 -3.4148;-7.1986 -3.6066 -2.8832;-5.9831 -3.4436 -3.6779;-6.3094 -3.8544 -3.2696;-6.2915 -5.4654 -4.1758;-6.5584 -4.4558 -3.2127;-5.8346 -3.3768 -2.5838];
Trọng số từ lớp ẩn đến lớp đầu ra.
Woh= [0.0188 -1.9734 0.6255 0.4932 -0.5925 -0.4435 1.0799 0.3705 -0.1926 -1.1629 -0.0350 -0.9390 0.3647 -0.6056 0.5726 -0.1639 -1.3403 -1.5193 -

1.6494 -1.8132 -0.2483; -0.0693 1.2123 1.3129 1.6006 0.7402 1.1716 1.5867 3.1500 2.3577 3.3629 2.4780 2.6302 2.9674 0.7661 1.5265 2.0676 1.7297 4.0159 2.3748 2.4173 2.9054;6.3216 3.3388 1.4826 -0.2754 -2.1694 -0.7430 -2.2963 -4.7001 -4.6418 -4.0895 -4.7556 -4.6468 -4.9112 -5.4908 -3.4376 -4.7539 -4.9947 -4.5363 -5.4131 -3.7736 -4.9652].
Số lượng đầu vào mạng nơ ron: Ni=2.
Số lượng đầu ra mạng nơ ron: No=3.
Số nơ ron trong lớp ẩn: Nh=20.
Hệ số tốc độ học: 0.7
Kết quả thực nghiệm:
Quá trình chạy thực nghiệm, nhóm tác giả có sử dụng thêm một bộ điều khiển Backstepping để tham chiếu và lấy kết quả so sánh. Video quá trình theo dõi và bám quĩ đạo của robot được thể hiện trong link đính kèm:
https://drive.google.com/drive/folders/1BHqT3GcOgGo_uNxxXz5bmAFDBDSqFcw2 (https://drive.google.com/drive/folders/1BHqT3GcOgGo_uNxxXz5bmAFDBDSqFcw2)


Hình 6. Tham số điều khiển được huấn luyện và chỉnh định theo điều kiện thực nghiệm


Hình 7. Quỹ đạo thực nghiệm.


Hình 8. Sai lệch đo được trong quá trình theo dõi quỹ đạo đặt
Các tham số điều khiển thay đổi liên tục trong quá trình thực nghiệm (hình 6), đảm bảo rằng robot có thể phản ứng nhanh chóng với các biến động từ môi trường và duy trì sự ổn định trong quá trình bám quỹ đạo. Điều này khẳng định khả năng tự học và thích nghi của bộ điều khiển dựa trên mạng nơ-ron.
Sai lệch bám rất nhỏ và không có sự dao động lớn trên hình 8, chứng minh rằng mạng nơ-ron đã giúp điều chỉnh và bù trừ sai lệch một cách hiệu quả, giúp duy trì sự ổn định của robot trong suốt quá trình vận hành. Từ hình 7, có thể thấy rằng sai số bám quỹ đạo của robot trung bình là 2.5%, với sai số tối đa trong các thử nghiệm là 3.2%. Nguyên nhân của các sai số này chủ yếu đến từ nhiễu ngẫu nhiên trong môi trường thực nghiệm và sự thay đổi bất thường trong điều kiện mặt đất. Tuy nhiên, nhờ khả năng tự học của mạng nơ-ron, bộ điều khiển đã nhanh chóng điều chỉnh tham số và giảm thiểu sai số xuống mức thấp nhất. Kết quả này cho thấy robot có thể thích ứng và duy trì độ chính xác cao trong điều kiện môi trường thực nghiệm.
Kết quả thực nghiệm cũng cho thấy bộ điều khiển mạng nơ-ron thích nghi đạt hiệu suất cao hơn so với Backstepping trong điều kiện thực tế:
Bộ điều khiển mạng nơ-ron có sai số bám quỹ đạo trung bình thấp hơn so với Backstepping, với mức sai số trung bình là 2.5% so với 3.8% của Backstepping. Thời gian hội tụ của bộ điều khiển mạng nơ-ron cũng ngắn hơn, trung bình 5 giây, trong khi Backstepping cần 7 giây để đạt độ ổn định. Điều này cho thấy khả năng phản ứng nhanh hơn của mạng nơ-ron đối với các thay đổi trong điều kiện môi trường.
V. KẾT LUẬN
Trong nghiên cứu này, chúng tôi đã phát triển và kiểm chứng một bộ điều khiển thích nghi dựa trên mạng nơ-ron cho WMR trong môi trường thực nghiệm. Bộ điều khiển này có khả năng tự học và thích nghi với các thay đổi của môi trường, giúp cải thiện đáng kể hiệu suất bám quỹ đạo và giảm sự phụ thuộc vào các mô hình động lực học phức tạp. Kết quả thực nghiệm đã cho thấy bộ điều khiển không chỉ đảm bảo độ chính xác cao trong quá trình bám quỹ đạo mà còn giúp robot hoạt động ổn định trong môi trường thực tế ngay cả khi hiểu biết về động lực học là hạn chế.

Việc sử dụng mạng nơ-ron để dự đoán và điều chỉnh các tham số điều khiển trong thời gian thực đã chứng minh hiệu quả vượt trội, với sai số trong quá trình bám quỹ đạo được giảm thiểu tối đa. Các kết quả từ hình 5, 6, và 7 cho thấy robot đã bám sát quỹ đạo với sai số rất nhỏ, đồng thời bộ điều khiển đã tự điều chỉnh linh hoạt để đảm bảo tính ổn định trong toàn bộ quá trình vận hành. Nghiên cứu này là tiền đề cho nhóm nghiên cứu phát triển các hệ thống điều khiển thông minh trong thời gian tới, khi khả năng tự học và thích nghi là yếu tố then chốt để đối phó với các thách thức từ môi trường thực tế.

VI. TÀI LIỆU THAM KHẢO

1. F. N. Martins, W. C. Celeste, R. Carelli, M. Sarcinelli-Filho, “A neural network-based adaptive controller for trajectory tracking of wheeled mobile robots,” IEEE Transactions on Neural Networks, vol. 19, no. 5, pp. 1178–1188, 2008.
2. S. Li, Y. Wang, Y. Luo, "Robust adaptive control for wheeled mobile robots using neural networks," Journal of Intelligent & Robotic Systems, vol. 50, pp. 169–183, 2007.
3. L. Li, T. Wang, Y. Xia, and N. Zhou, "Trajectory tracking control for wheeled mobile robots based on nonlinear disturbance observer with extended Kalman filter," Journal of the Franklin Institute, vol. 357, no. 15, pp. 8491–8507, 2020
4. Štefek, V. T. Pham, V. Krivanek, and K. L. Pham, "Optimization of Fuzzy Logic Controller Used for a Differential Drive Wheeled Mobile Robot," Applied Sciences, vol. 11, no. 13, pp. 6023, 2021.
5. P. Panahandeh, K. Alipour, B. Tarvirdizadeh, A. Hadi, “A kinematic Lyapunov-based controller to posture stabilization of wheeled mobile robots,” Mechanical Systems and Signal Processing, vol. 134, p. 106319, 2019.
6. Y. Guo, "Fuzzy control and neural network-based trajectory tracking for non-holonomic mobile robots," Journal of Control Engineering and Technology, vol. 12, no. 2, pp. 189–196, 2019.
7. M. Abdollahi, M. M. Baygi, M. A. Ahmadi, “Trajectory tracking control for mobile robots with neural network disturbance estimation,” International Journal of Robotics and Automation, vol. 33, pp. 129–136, 2015.
8. Rossi, M. Milani, “Trajectory tracking via robust adaptive control of a non-holonomic mobile robot,” Journal of Dynamic Systems, Measurement, and Control, vol. 140, 2018(2020-(J)_Controlling wh…).
9. Q. V. Dang, I. Nielsen, S. Bøgh, G. Bocewicz, “Modelling and scheduling autonomous mobile robot
for | a | real-world | industrial | application,” | IFAC
Proceedings Volumes, vol. 46(9), pp. 2098–2103, 2013.
10. Pazderski, “Application of transverse functions to control differentially driven wheeled robots using velocity fields,” Bulletin of the Polish Academy of Sciences: Technical Sciences, vol. 64.4, 2016.
11. L. Armesto, V. Girbés, A. Sala, M. Vicente, “Adaptive tracking for wheeled mobile robots using fuzzy logic,” International Journal of Approximate Reasoning, vol. 45, pp. 163–179, 2018.

12. H. S. Phuong, N. M. Tien, N. D. Tan, M. T. Anh and D.
D. Tu, "Proposal of a Fault-tolerant controller for wheeled mobile robots with faulty actuators", 12th

International Conference on Control, Automation and Information Sciences (ICCAIS), pp. 507-512, 2023.

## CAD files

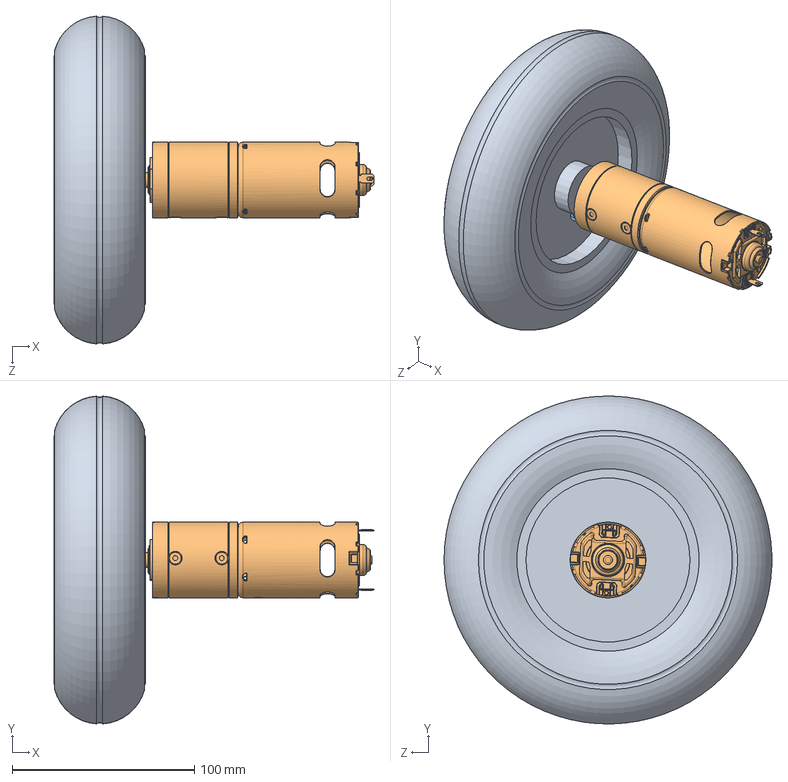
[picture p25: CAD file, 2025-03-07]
Solidworks/3D_SOLID/Assem2.SLDASM
175.5 x 179.9 x 179.9 mm
planet rs775 12-24V 60W 50RPM

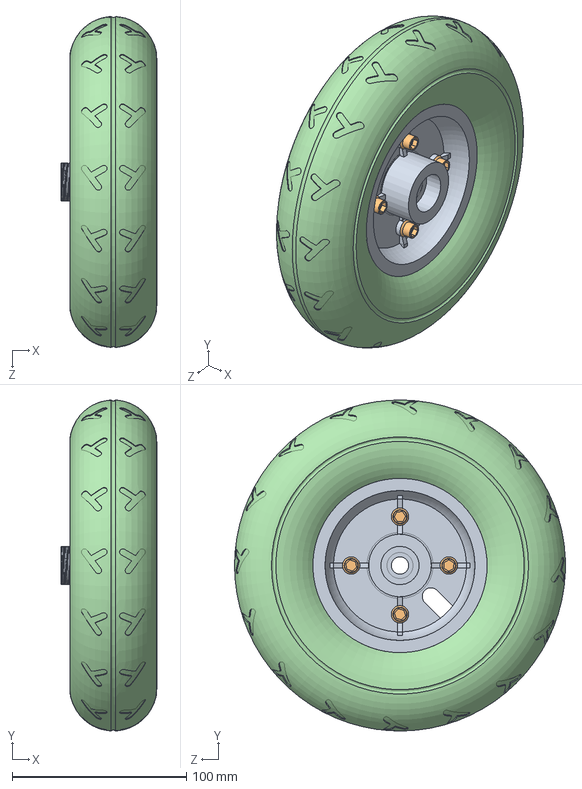
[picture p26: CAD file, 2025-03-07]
Solidworks/3D_SOLID/Assem8.SLDASM
55.0 x 189.9 x 190.0 mm
vanh

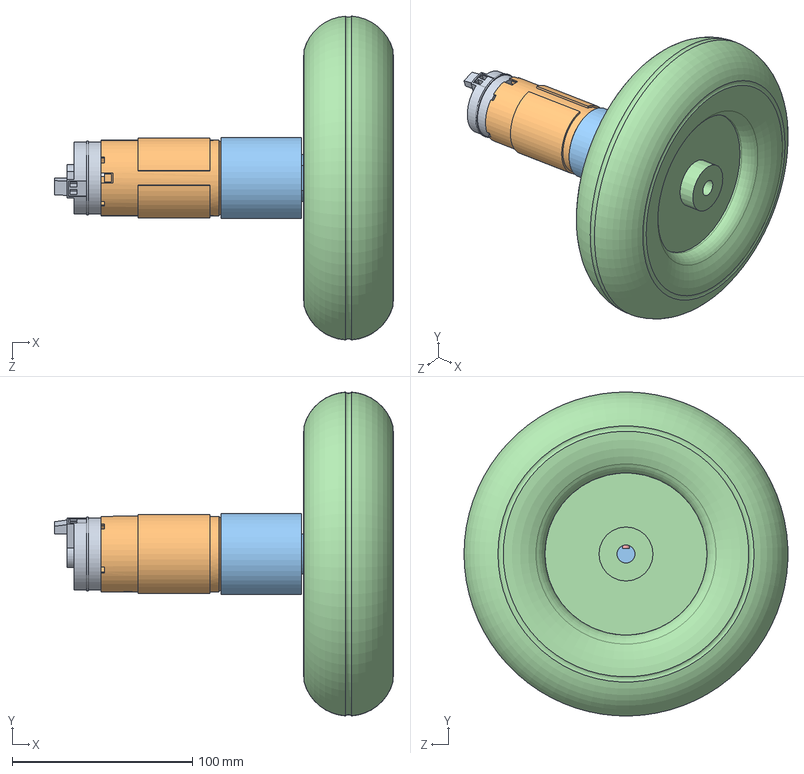
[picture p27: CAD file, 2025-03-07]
Solidworks/3D_SOLID/Assem1.SLDASM
188.3 x 179.9 x 179.9 mm
duoi
than
dau

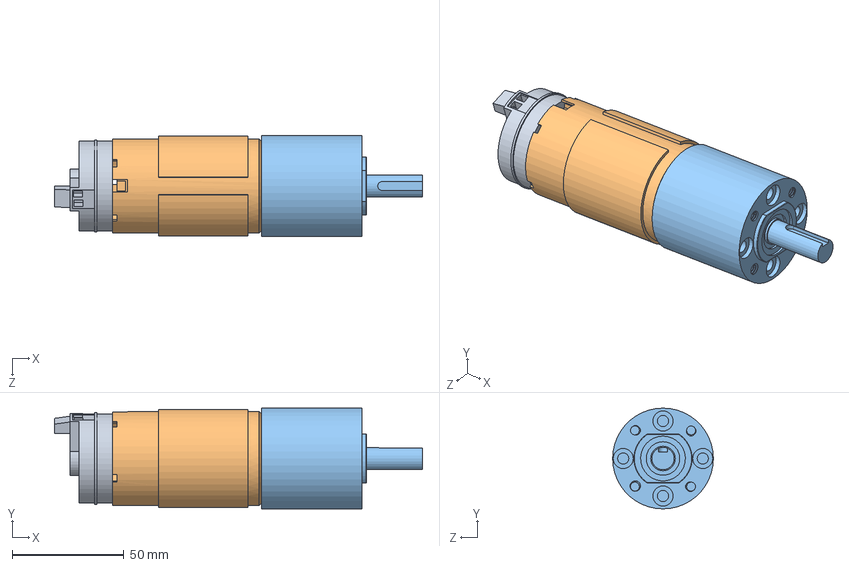
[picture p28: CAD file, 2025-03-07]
Solidworks/3D_SOLID/motor2.SLDASM
164.3 x 45.0 x 45.0 mm
duoi
than
dau

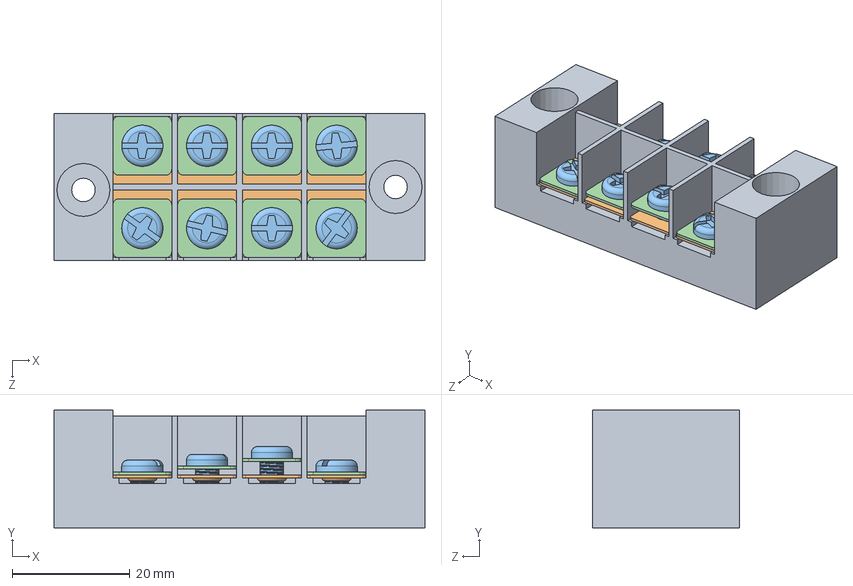
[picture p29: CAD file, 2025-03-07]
Solidworks/3D_SOLID/Assem4.SLDASM
63.0 x 20.0 x 25.0 mm

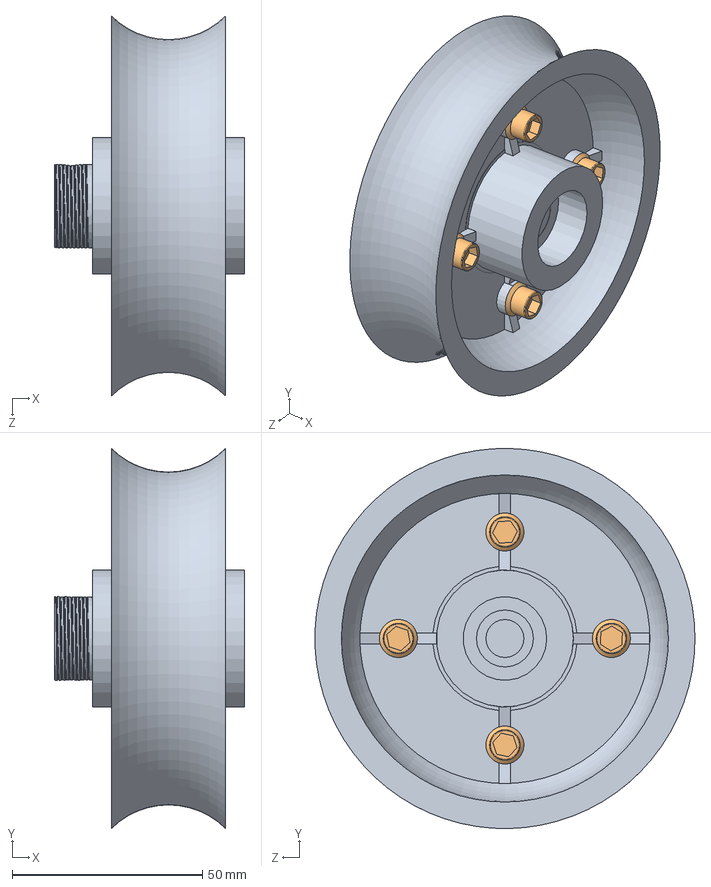
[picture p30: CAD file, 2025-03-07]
Solidworks/3D_SOLID/Assem7.SLDASM
50.0 x 100.0 x 100.0 mm
vanh

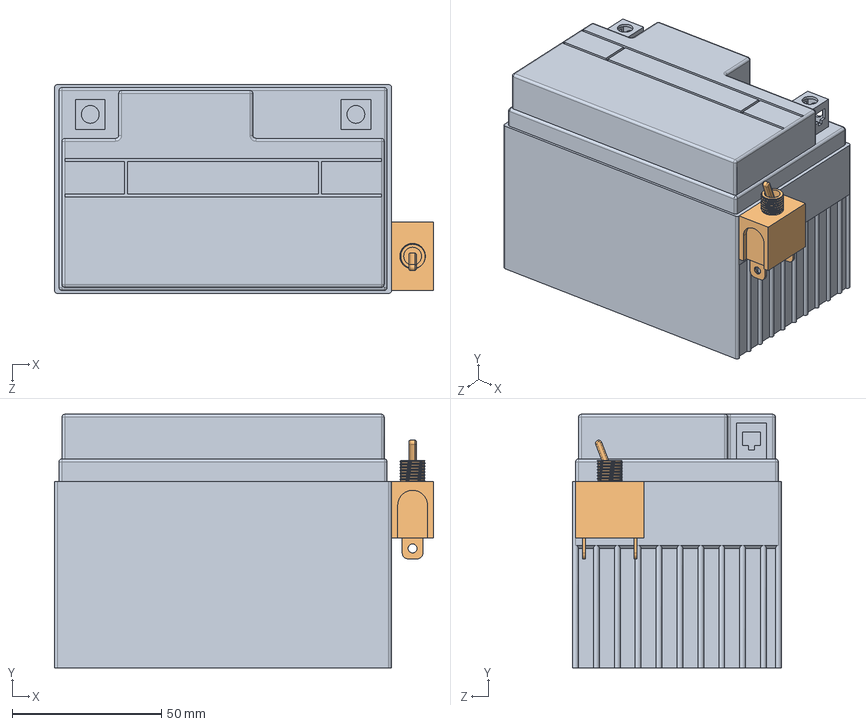
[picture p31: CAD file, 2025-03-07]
Solidworks/3D_SOLID/Assem9.SLDASM
127.0 x 85.0 x 70.0 mm

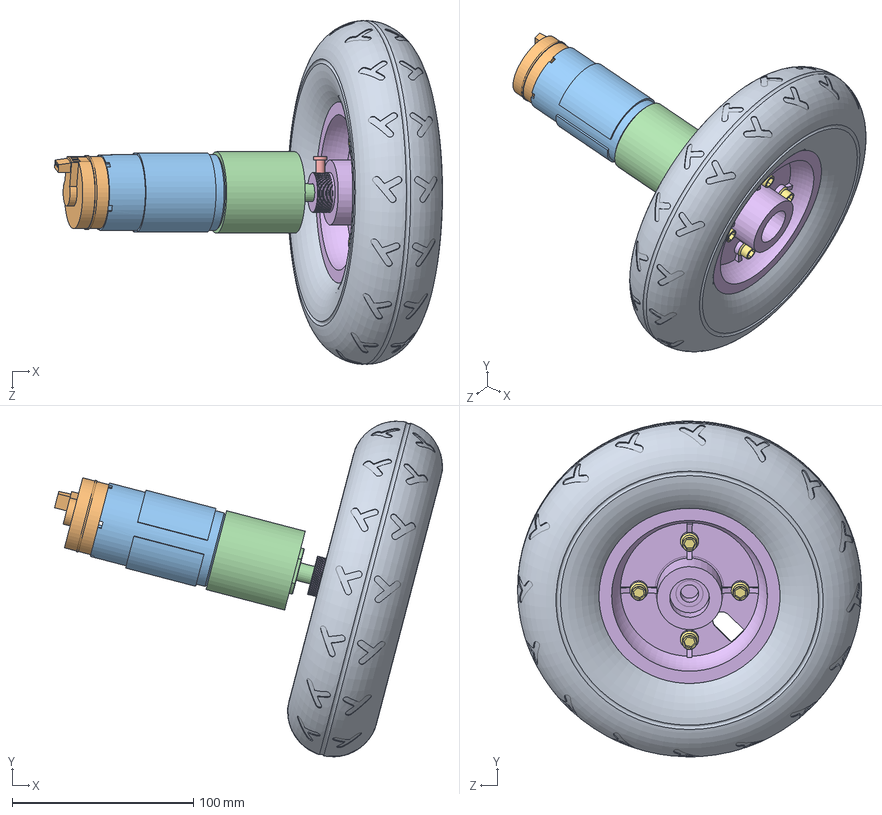
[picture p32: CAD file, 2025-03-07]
Solidworks/3D_SOLID/Assem6.SLDASM
214.3 x 185.4 x 189.9 mm
duoi
than
dau
vanh

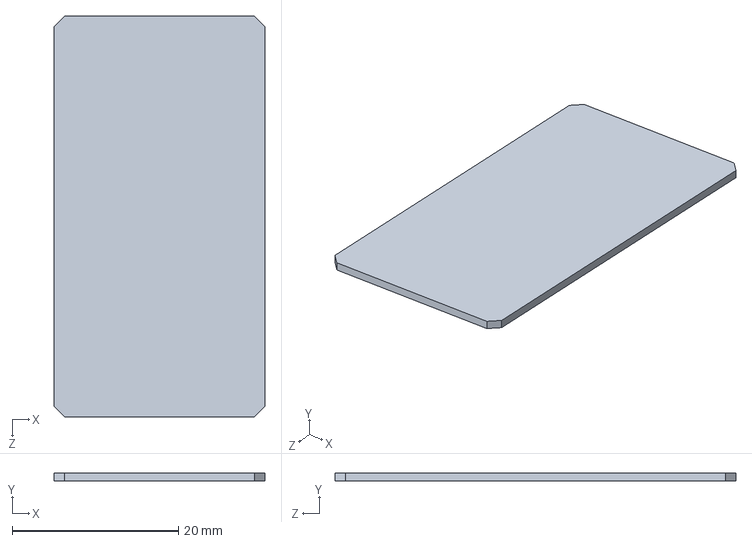
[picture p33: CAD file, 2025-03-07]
Solidworks/3D_SOLID/esp.SLDPRT
25.4 x 1.00 x 48.3 mm

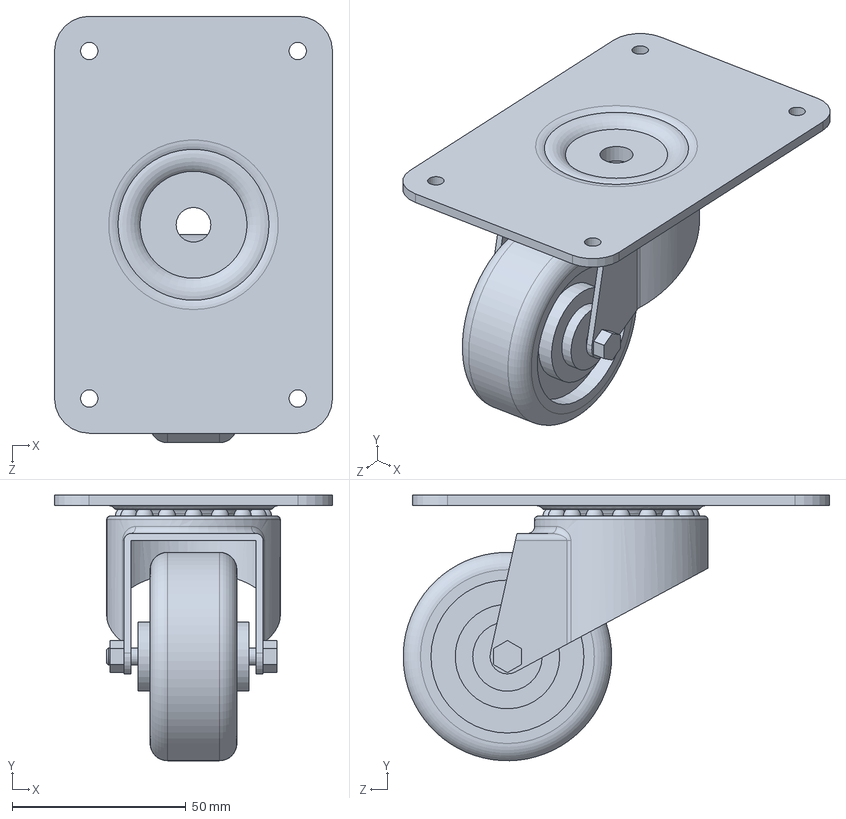
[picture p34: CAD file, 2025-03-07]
Solidworks/3D_SOLID/Part14.SLDPRT
80.0 x 76.4 x 122.7 mm

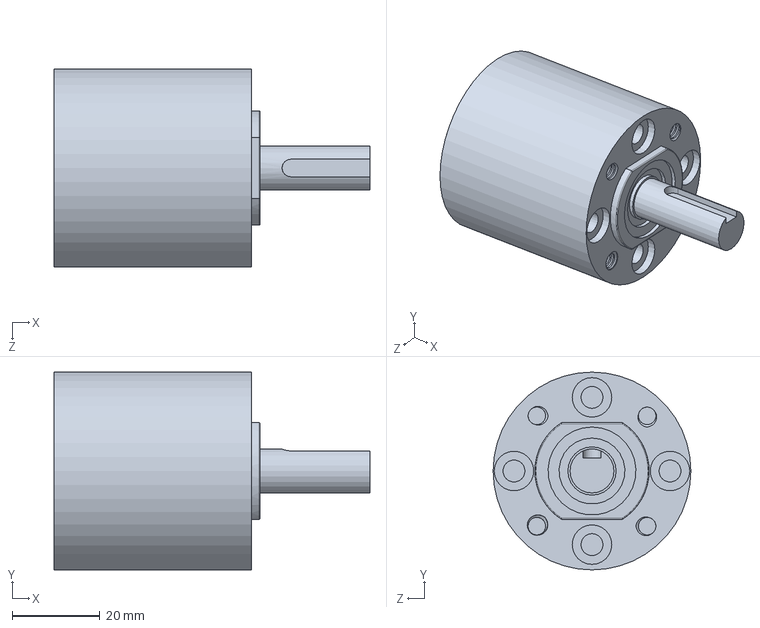
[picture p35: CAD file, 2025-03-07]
Solidworks/3D_SOLID/dau.SLDPRT
71.9 x 45.0 x 45.0 mm

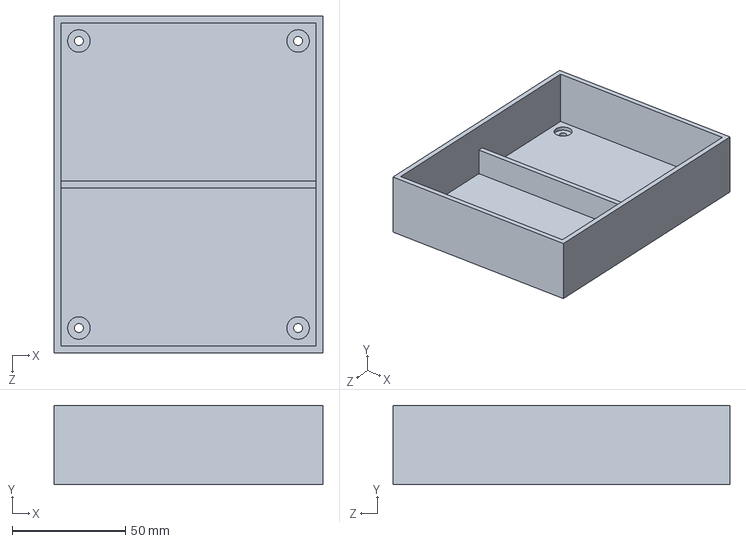
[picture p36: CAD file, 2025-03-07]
Solidworks/3D_SOLID/Part30.SLDPRT
119.0 x 35.0 x 149.0 mm

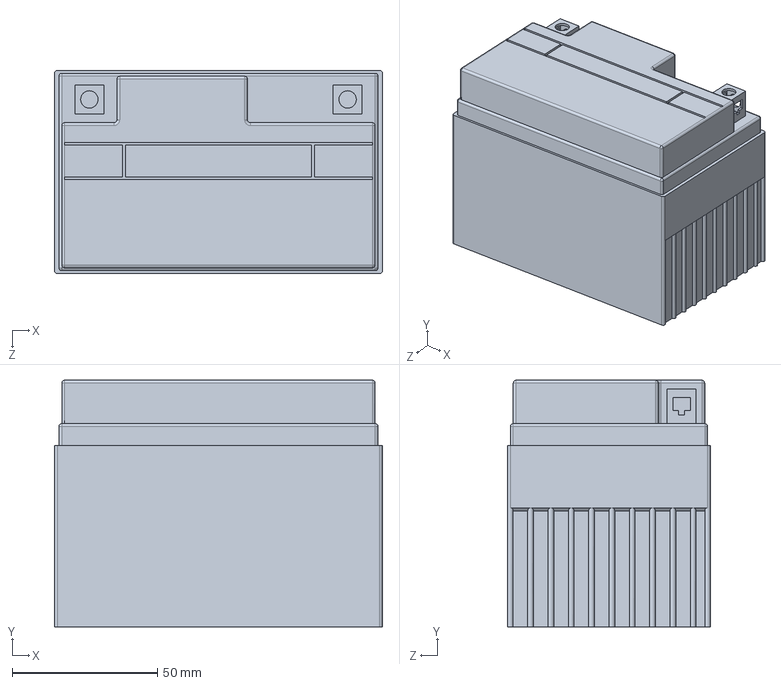
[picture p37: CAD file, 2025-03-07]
Solidworks/3D_SOLID/Part12.SLDPRT
113.0 x 85.0 x 70.0 mm

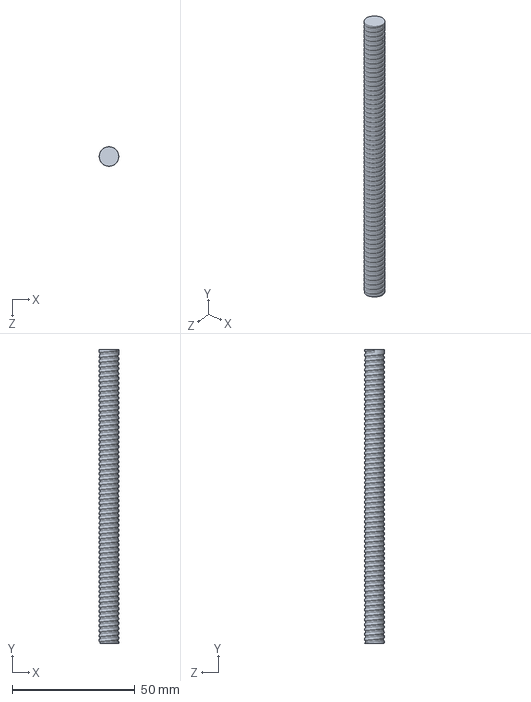
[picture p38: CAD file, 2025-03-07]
Solidworks/3D_SOLID/Part28.SLDPRT
8.00 x 120.0 x 8.00 mm

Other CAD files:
Solidworks/3D_SOLID/Part11.SLDPRT
Solidworks/3D_SOLID/motor.SLDPRT
Solidworks/3D_SOLID/Part10.SLDPRT
Solidworks/3D_SOLID/Part19.SLDPRT
Solidworks/3D_SOLID/Part1.SLDPRT
Solidworks/3D_SOLID/Part13.SLDPRT
Solidworks/3D_SOLID/Part15.SLDPRT
Solidworks/3D_SOLID/Part16.SLDPRT
Solidworks/3D_SOLID/Part17.SLDPRT
Solidworks/3D_SOLID/Part18.SLDPRT
Solidworks/3D_SOLID/Part20.SLDPRT
Solidworks/3D_SOLID/Part21.SLDPRT
Solidworks/3D_SOLID/Part22.SLDPRT
Solidworks/3D_SOLID/Part23.SLDPRT
Solidworks/3D_SOLID/Part24.SLDPRT
Solidworks/3D_SOLID/Part25.SLDPRT
Solidworks/3D_SOLID/Part26.SLDPRT
Solidworks/3D_SOLID/Part27.SLDPRT
Solidworks/3D_SOLID/Part29.SLDPRT
Solidworks/3D_SOLID/Part31.SLDPRT
Solidworks/3D_SOLID/Part32.SLDPRT
Solidworks/3D_SOLID/Part33.SLDPRT
Solidworks/3D_SOLID/Part34.SLDPRT
Solidworks/3D_SOLID/Part35.SLDPRT
Solidworks/3D_SOLID/Part36.SLDPRT
Solidworks/3D_SOLID/Part37.SLDPRT
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

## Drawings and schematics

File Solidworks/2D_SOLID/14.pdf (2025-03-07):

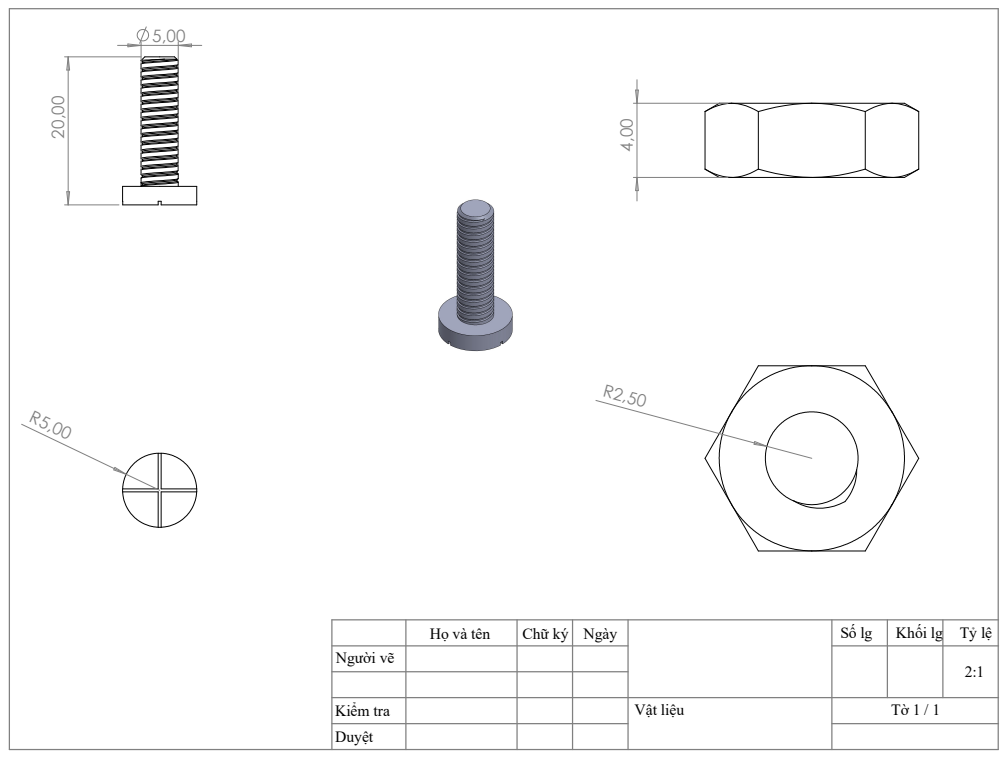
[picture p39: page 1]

Họ và tên | Chữ ký | Ngày | Số lg | Khối lg | Tỷ lệ

Người vẽ | | | | | | 2:1

Kiểm tra | Vật liệu | Tờ 1 / 1
Duyệt

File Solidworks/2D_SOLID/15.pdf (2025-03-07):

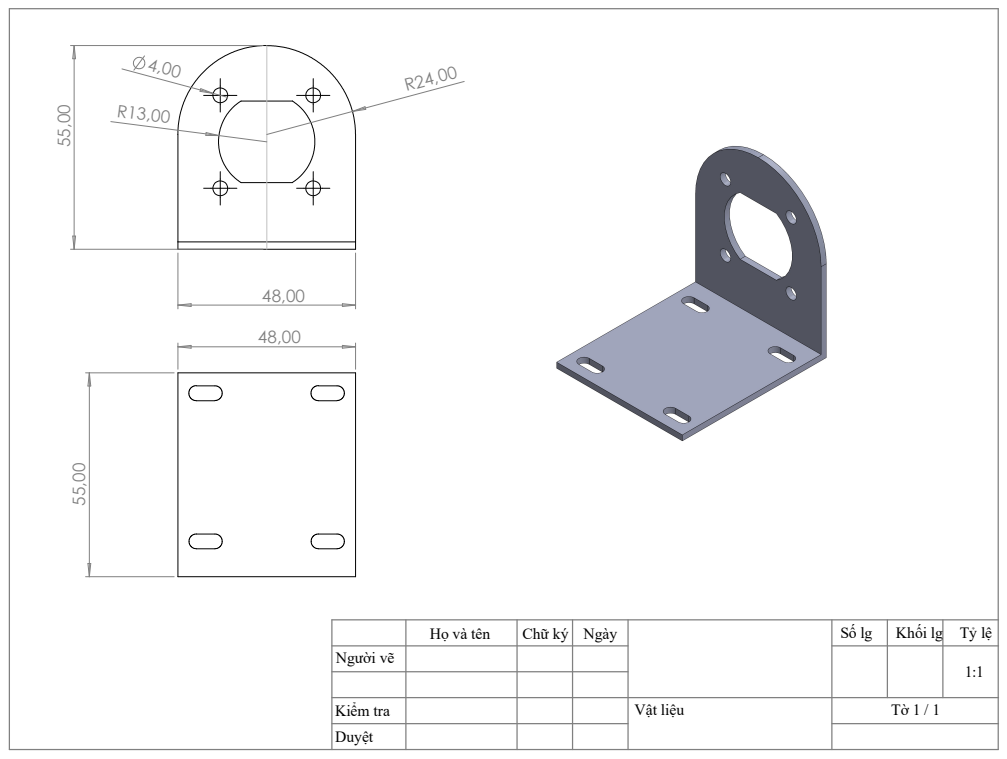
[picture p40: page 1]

Vật liệu ⁵⁵,00

Họ và tên | Chữ ký | Ngày | Số lg | Khối lg | Tỷ lệ

Người vẽ | | | | | | 1:1

Kiểm tra | Tờ 1 / 1
Duyệt

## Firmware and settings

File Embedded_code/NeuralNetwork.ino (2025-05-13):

/*******************************************************************************
 * Two-Wheeled Mobile Robot Neural Network Controller
 * 
 * This file implements a Neural Network controller for trajectory tracking 
 * of a two-wheeled differential drive mobile robot using ESP32.
 * 
 * Features:
 * - Real-time trajectory tracking using Neural Network controller
 * - Wi-Fi connectivity for remote monitoring and control
 * - Web interface for visualization and parameter adjustment
 * - Online learning with backpropagation algorithm
 * - Hardware interface for motors and encoders
 * 
 * Hardware:
 * - ESP32 microcontroller
 * - DC motors with encoders (249.6 ticks per revolution)
 * - Wheel diameter: 19 cm
 * - Wheelbase: 38 cm
 * 
 * Dependencies:
 * - WiFi.h
 * - WebServer.h
 * - MatrixMath.h
 * 
 * Usage:
 * 1. Set the SSID and password in the code
 * 2. Upload to ESP32
 * 3. Connect to the ESP32's IP address with a web browser
 * 4. Use the web interface to start/stop the robot and monitor performance
 * 
 *******************************************************************************/

#include <WiFi.h>
#include <WebServer.h>
#include <MatrixMath.h>

//=============================================================================
// CONFIGURATION PARAMETERS
//=============================================================================

// WiFi Configuration
const char* ssid = " ";      // WiFi SSID - to be filled before uploading
const char* password = " ";  // WiFi Password - to be filled before uploading

// Controller Parameters
float kp = 0.02;     // Proportional gain for PID
float ki = 0.00015;  // Integral gain for PID
float kd = 0.01;     // Derivative gain for PID

// Robot Dimensions
float l = 0.38;      // Wheelbase (distance between wheels) in meters
float d = 0.19;      // Wheel diameter in meters

//=============================================================================
// HARDWARE PINS
//=============================================================================

// Motor 1 Pins (Right Motor)
int motor1Pin1 = 2;   // Motor driver input 1
int motor1Pin2 = 4;   // Motor driver input 2
int enable1Pin = 12;  // Motor driver enable pin

// Motor 2 Pins (Left Motor)
int motor2Pin1 = 19;  // Motor driver input 1
int motor2Pin2 = 18;  // Motor driver input 2
int enable2Pin = 15;  // Motor driver enable pin

// Encoder Pins
int encoA_motor1 = 26;  // Encoder A for motor 1
int encoB_motor1 = 13;  // Encoder B for motor 1
int encoA_motor2 = 32;  // Encoder A for motor 2
int encoB_motor2 = 14;  // Encoder B for motor 2

// PWM Configuration
const int freq = 30000;     // PWM frequency
const int pwmChannel = 0;   // PWM channel for motor 1
const int resolution = 8;   // PWM resolution (8-bit = 0-255)

//=============================================================================
// GLOBAL VARIABLES
//=============================================================================

// Timer Variables
hw_timer_t *timer1 = NULL;
volatile unsigned long count = 0;
unsigned long count_prev = 0;

// Transformation Matrices
mtx_type Td[2][2];     // Transformation matrix
mtx_type TdInv[2][2];  // Inverse transformation matrix

// Motion Variables
float vantoc = 0;    // Velocity
float vthuc = 0;     // Actual velocity
float quangduong1 = 0;  // Distance traveled by wheel 1
float quangduong2 = 0;  // Distance traveled by wheel 2
float quangduongthuc = 0;  // Actual distance traveled

// Angular Position Variables
float Theta_now1;    // Current angular position of motor 1
float Theta_prev1 = 0;  // Previous angular position of motor 1
float Theta_now2;    // Current angular position of motor 2
float Theta_prev2 = 0;  // Previous angular position of motor 2

// Velocity and RPM Variables
float Vl_output;     // Left wheel velocity output
float RPM_output1, RPM_input1;  // RPM for motor 1
float Vr_output;     // Right wheel velocity output
float RPM_output2, RPM_input2;  // RPM for motor 2

// Time Variables
float dt1;           // Delta time for motor 1 control
float dt2;           // Delta time for motor 2 control
unsigned long t_prev = 0;   // Previous time
unsigned long t_now1;       // Current time for motor 1
unsigned long t_prev1 = 0;  // Previous time for motor 1
unsigned long t_now2;       // Current time for motor 2
unsigned long t_prev2 = 0;  // Previous time for motor 2

// Encoder Counters
volatile long dem_motor1 = 0;    // Motor 1 encoder counter (total)
volatile long dem_motor2 = 0;    // Motor 2 encoder counter (total)
volatile long dem_motor11 = 0;   // Motor 1 encoder counter (direction-sensitive)
volatile long dem_motor22 = 0;   // Motor 2 encoder counter (direction-sensitive)

// Motor Control Variables
int PWMval1 = 0;     // PWM value for motor 1
int PWMval2 = 0;     // PWM value for motor 2
float Vmax = 24;     // Maximum voltage
float Vmin = 0;      // Minimum voltage
float V1 = 0;        // Voltage for motor 1
float V2 = 0;        // Voltage for motor 2

// PID Control Variables
float error_now1, error_prev1 = 0, integ_now1, integ_prev1 = 0;  // PID variables for motor 1
float error_now2, error_prev2 = 0, integ_now2, integ_prev2 = 0;  // PID variables for motor 2

// Wheel Velocity Variables
float globalVL = 0;    // Left wheel velocity command
float globalVR = 0;    // Right wheel velocity command
float globalVLL = 0;   // Processed left wheel velocity
float globalVRR = 0;   // Processed right wheel velocity
float leftWheelSpeedpre = 0;   // Previous left wheel speed
float rightWheelSpeedpre = 0;  // Previous right wheel speed

// Robot State Variables
float v = 0, w = 0;    // Linear and angular velocity
float x = 0, y = 0;    // Robot position
float toadox = 0, toadoy = 0;  // Position in cm
float theta = 0;       // Robot orientation

// Trajectory Variables
float t = 0;           // Time variable for trajectory
float omega = 0.25;    // Angular frequency for circular trajectory
float R = 122;         // Radius of circular trajectory (cm)
bool check = false;    // Flag for trajectory following

// Trajectory Tracking Variables
float xd = 0, yd = 0;  // Desired position
float xd_dot = 0, yd_dot = 0;  // Desired velocity
float xd_2dot = 0, yd_2dot = 0;  // Desired acceleration
float Theta = 0, Thetad = 0, Theta0 = 0;  // Orientation variables
float x1d = 0, y1d = 0, x1d_dot = 0, y1d_dot = 0;  // Reference point variables
float wd = 0;          // Desired angular velocity
float V = 0, W = 0;    // Linear and angular velocity commands
float VL = 0, VR = 0;  // Left and right wheel velocity commands
float X1 = 0, Y1 = 0;  // Reference point position
float ex = 0, ey = 0, eth = 0;  // Position and orientation errors
float xe = 0, ye = 0, thetae = 0;  // Transformed errors
float Vc = 0, Wc = 0;  // Control inputs
float vt = 0, vp = 0;  // Tangential and normal velocities
float x0d_dot = 0, y0d_dot = 0;  // Initial desired velocities
float xdat = 0, ydat = 0;  // Desired position in cm
float b = 0.03;        // Distance to reference point
float Kx = 0.0, Ky = 0.0, Kth = 0.0;  // Control gains
float pi = 3.14;       // Pi constant
float wthuc = 0;       // Actual angular velocity
float vr = 0;          // Reference linear velocity
float wr = 0;          // Reference angular velocity

//=============================================================================
// NEURAL NETWORK PARAMETERS
//=============================================================================

// Neural Network Architecture
int Ni = 2;            // Number of input neurons
int No = 3;            // Number of output neurons
int Nh = 20;           // Number of hidden neurons

// Neural Network Weights
float Whi[20][3] = {   // Hidden layer weights (20x3)
  {-6.4855, -4.0100, -4.5498}, {-6.5890, -4.7984, -2.1504}, {-6.5339, -3.9266, -4.3257}, {-7.4260, -3.7515, -2.3720}, 
  {-6.3217, -4.2807, -3.3511}, {-6.1753, -4.2071, -3.1082}, {-8.9702, -5.8552, -4.7596}, {-7.3099, -6.6322, -4.5009}, 
  {-6.2155, -5.9031, -5.4120}, {-5.9862, -3.5501, -3.1355}, {-5.9129, -4.1946, -3.8804}, {-6.3110, -4.0644, -2.8849}, 
  {-6.2365, -2.9500, -2.3163}, {-8.2328, -6.5682, -3.4148}, {-7.1986, -3.6066, -2.8832}, {-5.9831, -3.4436, -3.6779}, 
  {-6.3094, -3.8544, -3.2696}, {-6.2915, -5.4654, -4.1758}, {-6.5584, -4.4558, -3.2127}, {-5.8346, -3.3768, -2.5838}
};

float Woh[3][21] = {   // Output layer weights (3x21)
  {0.0188, -1.9734, 0.6255, 0.4932, -0.5925, -0.4435, 1.0799, 0.3705, -0.1926, -1.1629, -0.0350, -0.9390, 0.3647, -0.6056, 0.5726, -0.1639, -1.3403, -1.5193, -1.6494, -1.8132, -0.2483},
  {-0.0693, 1.2123, 1.3129, 1.6006, 0.7402, 1.1716, 1.5867, 3.1500, 2.3577, 3.3629, 2.4780, 2.6302, 2.9674, 0.7661, 1.5265, 2.0676, 1.7297, 4.0159, 2.3748, 2.4173, 2.9054},
  {6.3216, 3.3388, 1.4826, -0.2754, -2.1694, -0.7430, -2.2963, -4.7001, -4.6418, -4.0895, -4.7556, -4.6468, -4.9112, -5.4908, -3.4376, -4.7539, -4.9947, -4.5363, -5.4131, -3.7736, -4.9652}
};

// Learning Parameters
float eta = 0.7;       // Learning rate
float beta = 0.3;      // Momentum coefficient

// Weight Update Variables
double Woh_old[3][21];  // Previous output layer weights
double DWoh[3][21];     // Output layer weight changes
double DWhi[20][3];     // Hidden layer weight changes
double Dold = 0;        // Previous weight change (output layer)
double Doldi = 0;       // Previous weight change (hidden layer)

// State Variables for Learning
double x_old = 0.0;     // Previous x position
double y_old = 0.0;     // Previous y position
double theta_old = 0.0;  // Previous orientation
double vc_old = 0.0;     // Previous linear velocity command
double wc_old = 0.0;     // Previous angular velocity command

// Control Gain Adaptation
double Kx_old = 1.3;    // Previous x gain
double Ky_old = 2.5;    // Previous y gain
double Kth_old = 1.2;   // Previous orientation gain

double etaX = 0.01;     // Learning rate for x gain
double etaY = 0.01;     // Learning rate for y gain
double etaTh = 0.01;    // Learning rate for orientation gain

double DKx_old = 0;     // Previous x gain change
double DKy_old = 0;     // Previous y gain change
double DKth_old = 0;    // Previous orientation gain change

double Betax = 0.01;    // Momentum coefficient for x gain
double Betay = 0.01;    // Momentum coefficient for y gain
double Betath = 0.01;   // Momentum coefficient for orientation gain

// Jacobian Matrix Elements
double Jacv11 = 0, Jacv12 = 0;  // Jacobian elements for x
double Jacv21 = 0, Jacv22 = 0;  // Jacobian elements for y
double Jacv31 = 0, Jacv32 = 0;  // Jacobian elements for orientation

// Web Server
WebServer server(80);   // Web server on port 80

void IRAM_ATTR dem_xung_motor1() {
  if (digitalRead(encoB_motor1) == HIGH) {
    dem_motor1++;
    dem_motor11++;
  } else {
    dem_motor1++;
    dem_motor11--;
  }
}

void IRAM_ATTR dem_xung_motor2() {
  if (digitalRead(encoB_motor2) == HIGH) {
    dem_motor2++;
    dem_motor22++;
  } else {
    dem_motor2++;
    dem_motor22--;
  }
}

/**
 * @brief Timer interrupt handler
 * Increments the counter for timing control loops
 */
void IRAM_ATTR onTimer1() {
  count++;
}

//=============================================================================
// SETUP FUNCTION
//=============================================================================

/**
 * @brief Setup function - runs once at startup
 * Initializes pins, interrupts, timer, WiFi, and web server
 */
void setup() {
  // Initialize serial communication
  Serial.begin(9600);
  
  // Configure motor pins
  pinMode(motor1Pin1, OUTPUT);
  pinMode(motor1Pin2, OUTPUT);
  pinMode(enable1Pin, OUTPUT);
  pinMode(motor2Pin1, OUTPUT);
  pinMode(motor2Pin2, OUTPUT);
  pinMode(enable2Pin, OUTPUT);
  
  // Configure PWM
  ledcSetup(pwmChannel, freq, resolution);
  ledcSetup(pwmChannel + 1, freq, resolution);
  ledcAttachPin(enable1Pin, pwmChannel);
  ledcAttachPin(enable2Pin, pwmChannel + 1);

  // Configure encoder pins
  pinMode(encoA_motor1, INPUT);
  pinMode(encoB_motor1, INPUT);
  pinMode(encoA_motor2, INPUT);
  pinMode(encoB_motor2, INPUT);
  
  // Attach interrupt handlers to encoder pins
  attachInterrupt(digitalPinToInterrupt(encoA_motor1), dem_xung_motor1, RISING);
  attachInterrupt(digitalPinToInterrupt(encoA_motor2), dem_xung_motor2, RISING);
  
  // Configure timer for 150ms intervals (6.67 Hz)
  timer1 = timerBegin(0, 80, true);  // 80MHz clock divided by 80 = 1MHz
  timerAttachInterrupt(timer1, &onTimer1, true); 
  timerAlarmWrite(timer1, 150000, true);  // 150000 ticks = 150ms
  timerAlarmEnable(timer1); 

  // Connect to WiFi
  WiFi.begin(ssid, password);
  while (WiFi.status() != WL_CONNECTED) {
    Serial.println("Connecting to WiFi...");
    delay(500);
  }

  // Print connection info
  Serial.println("WiFi connected");
  Serial.print("IP address: ");
  Serial.println(WiFi.localIP());

  // Configure web server routes
  server.on("/", handleRoot);        // Root page - displays status
  server.on("/start", handleStart);  // Start trajectory following
  server.on("/stop", stop);          // Stop robot
  server.on("/reset", reset);        // Reset robot state
  server.begin();
  Serial.println("HTTP server started");
}

//=============================================================================
// MAIN LOOP
//=============================================================================

/**
 * @brief Main loop function - runs repeatedly
 * Handles web client requests, calculates position, and controls motors
 */
void loop() {
  // Handle web client requests
  server.handleClient();
  
  // Update robot position
  tinhtoado();

  // Safety check - stop motors if commanded velocity is zero
  if (globalVLL == 0) {
    ledcWrite(pwmChannel + 1, 0);
  }
  if (globalVRR == 0) {
    ledcWrite(pwmChannel, 0);
  }
  
  // Run control loop at fixed intervals (triggered by timer)
  if (count > count_prev) {
    // Generate desired trajectory
    quydao();
    
    // Update time measurements
    t_now1 = millis();
    t_now2 = millis();
    dt1 = (t_now1 - t_prev1);
    dt2 = (t_now2 - t_prev2);
    
    // Execute PID controllers for both motors
    PID1();
    PID2();
    
    // Execute Neural Network controller
    NeuralNetwork();
    
    // Calculate actual robot velocity and angular velocity
    vthuc = (Vl_output + Vr_output) / 2;
    wthuc = (Vr_output - Vl_output) / l;
    
    // Store current time for next iteration
    t_prev1 = t_now1;
    t_prev2 = t_now2;
    count_prev = count;
  }
}

//=============================================================================
// POSITION CALCULATION
//=============================================================================

/**
 * @brief Calculate robot position based on wheel encoder readings
 * Uses kinematics equations to determine position and orientation
 */
void tinhtoado() {
  // Calculate time since last update
  unsigned long currentTime = millis();
  float deltaTime = (currentTime - prevTime) / 1000.0;  // Convert to seconds
  
  // Calculate wheel speeds from encoder counts
  float leftWheelSpeed = (dem_motor22 / 249.6) * 3.14 * 0.19;   // Speed in m/s
  float rightWheelSpeed = (dem_motor11 / 249.6) * 3.14 * 0.19;  // Speed in m/s
  
  // Calculate robot linear and angular velocity
  v = (rightWheelSpeed + leftWheelSpeed) / 2;  // Linear velocity
  w = (rightWheelSpeed - leftWheelSpeed) / l;  // Angular velocity
  
  // Update robot orientation
  theta = theta + w;
  
  // Update robot position using the kinematic model
  x = x + v * cos(theta + (w / 2));
  y = y + v * sin(theta + (w / 2));

  // Convert position to centimeters for display
  toadox = x * 100;
  toadoy = y * 100;
  
  // Reset encoder counters for next calculation
  dem_motor11 = 0;
  dem_motor22 = 0;
  
  // Save current time for next calculation
  prevTime = currentTime;
}

//=============================================================================
// WEB SERVER HANDLERS
//=============================================================================

/**
 * @brief Handle root web page request
 * Returns JSON with current robot state and parameters
 */
void handleRoot() {
  // Create JSON string with current robot state
  String motorData = "{\"Kx\":" + String(Kx) +
                     ",\"Ky\":" + String(Ky) +
                     ",\"Kth\":" + String(Kth) +
                     ",\"toadox\":" + String(toadox) +
                     ",\"toadoy\":" + String(toadoy) +
                     ",\"xdat\":" + String(xdat) +
                     ",\"ydat\":" + String(ydat) +
                     ",\"theta\":" + String(theta) +
                     ",\"Thetad\":" + String(Thetad) +
                     ",\"Vc\":" + String(Vc) +
                     ",\"Wc\":" + String(Wc) +
                     ",\"ex\":" + String(ex * 100.0) +
                     ",\"ey\":" + String(ey * 100.0) +
                     ",\"eth\":" + String(eth) +
                     ",\"t\":" + String(t) +
                     "}";
  
  // Send JSON response
  server.send(200, "application/json", motorData);
}

/**
 * @brief Handle start command
 * Sets the flag to start trajectory following
 */
void handleStart() {
  check = true;
  server.send(200, "text/html", "started");
}

/**
 * @brief Handle stop command
 * Stops the robot by setting velocities to zero
 */
void stop() {
  // Stop trajectory following
  check = false;
  
  // Set velocities to zero
  globalVRR = 0;
  globalVLL = 0;
  RPM_input1 = 0;
  RPM_input2 = 0;
  
  // Send response
  server.send(200, "text/html", "stop");
}

/**
 * @brief Handle reset command
 * Resets robot state variables
 */
void reset() {
  // Reset could be implemented to zero position, orientation, etc.
  server.send(200, "text/html", "reset");
}

//=============================================================================
// TRAJECTORY GENERATION
//=============================================================================

/**
 * @brief Generate circular trajectory and calculate control inputs
 * Implements trajectory tracking controller based on kinematic model
 */
void quydao() {
  if (check == true) {
    // Generate circular trajectory
    xdat = (R) * cos(omega * t);                  // Desired x position in cm
    ydat = (R) * sin(omega * t);                  // Desired y position in cm
    xd = (R / 100) * cos(omega * t);              // Desired x position in m
    yd = (R / 100) * sin(omega * t);              // Desired y position in m
    xd_dot = -(R / 100) * omega * sin(omega * t); // Desired x velocity
    yd_dot = (R / 100) * omega * cos(omega * t);  // Desired y velocity
    x0d_dot = -(R / 100) * omega * sin(omega);    // Initial x velocity
    y0d_dot = (R / 100) * omega * cos(omega);     // Initial y velocity
    xd_2dot = -(R / 100) * omega * omega * cos(omega * t); // Desired x acceleration
    yd_2dot = -(R / 100) * omega * omega * sin(omega * t); // Desired y acceleration
    
    // Calculate desired orientation
    Theta0 = atan2(y0d_dot, x0d_dot) - omega;
    Thetad = omega * t + Theta0;
    
    // Calculate reference point position (offset by b)
    x1d = xd + b * cos(Thetad);
    y1d = yd + b * sin(Thetad);
    
    // Calculate desired angular velocity
    wd = (yd_2dot * xd_dot - xd_2dot * yd_dot) / (xd_dot * xd_dot + yd_dot * yd_dot);
    
    // Calculate reference point velocities
    x1d_dot = xd_dot - b * wd * sin(Thetad);
    y1d_dot = yd_dot + b * wd * cos(Thetad);
    
    // Calculate transformation matrix
    Td[0][0] = cos((Thetad));
    Td[0][1] = -b * sin((Thetad));
    Td[1][0] = sin((Thetad));
    Td[1][1] = b * cos((Thetad));
    
    // Calculate inverse transformation matrix
    Matrix.Invert((mtx_type*)Td, 2);
    Matrix.Copy((mtx_type*)Td, 2, 2, (mtx_type*)TdInv);
    
    // Calculate reference linear and angular velocities
    vr = TdInv[0][0] * x1d_dot + TdInv[0][1] * y1d_dot;
    wr = TdInv[1][0] * x1d_dot + TdInv[1][1] * y1d_dot;
    
    // Calculate actual reference point position
    X1 = x + b * cos(theta);
    Y1 = y + b * sin(theta);

    // Calculate position and orientation errors
    ex = xd - x;
    ey = yd - y;
    eth = Thetad - theta;

    // Transform errors to robot frame
    xe = cos((theta)) * ex + sin((theta)) * ey;
    ye = -sin((theta)) * ex + cos((theta)) * ey;
    thetae = eth;

    // Calculate control inputs (linear and angular velocity commands)
    Vc = vr * cos(thetae) + Kx * xe;
    Wc = wr + vr * Ky * ye + Kth * sin(thetae);

    // Calculate wheel velocity commands
    globalVRR = (2 * Vc + (l * (Wc))) / 2;
    globalVLL = 2 * Vc - globalVRR;
    
    // Increment time
    t = t + 0.15;
  }
}

//=============================================================================
// MOTOR CONTROL
//=============================================================================
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

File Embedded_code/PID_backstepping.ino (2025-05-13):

#include <WiFi.h>
#include <WebServer.h>
#include <MatrixMath.h>

// Cấu trúc lưu trữ dữ liệu liên quan đến robot
struct RobotData {
  float x = 0, y = 0, theta = 0;
  float toadox = 0, toadoy = 0;
  float vthuc = 0, wthuc = 0;
  float ex = 0, ey = 0, eth = 0;
};

// Cấu trúc lưu trữ dữ liệu liên quan đến PID
struct PIDData {
  float kp = 0.02;
  float ki = 0.00015;
  float kd = 0.01;
  float error_now1 = 0, error_prev1 = 0, integ_now1 = 0, integ_prev1 = 0;
  float error_now2 = 0, error_prev2 = 0, integ_now2 = 0, integ_prev2 = 0;
};

// Cấu trúc lưu trữ dữ liệu liên quan đến quỹ đạo
struct TrajectoryData {
  float xd = 0, yd = 0;
  float xd_dot = 0, yd_dot = 0;
  float xd_2dot = 0, yd_2dot = 0;
  float Thetad = 0, Theta0 = 0;
  float x1d = 0, y1d = 0;
  float x1d_dot = 0, y1d_dot = 0;
  float wd = 0;
  float vr = 0, wr = 0;
  float Vc = 0, Wc = 0;
  float xdat = 0, ydat = 0;
};

// Khởi tạo các cấu trúc
RobotData robot;
PIDData pid;
TrajectoryData traj;

mtx_type Td[2][2];
mtx_type TdInv[2][2];

// Thông số WiFi
const char* ssid = "VinhUni";
const char* password = "1111111111";

// Timer
hw_timer_t *timer1 = NULL;

// Pins động cơ
const int motor1Pin1 = 2;
const int motor1Pin2 = 4;
const int enable1Pin = 12;
const int motor2Pin1 = 19;
const int motor2Pin2 = 18;
const int enable2Pin = 15;

// Thiết lập PWM
const int freq = 30000;
const int pwmChannel = 0;
const int resolution = 8;

// Pins encoder
const int encoA_motor1 = 26;
const int encoB_motor1 = 13;
const int encoA_motor2 = 32;
const int encoB_motor2 = 14;

// Thông số robot
float quangduong1 = 0;
float quangduong2 = 0;
float quangduongthuc = 0;
const float l = 0.38;  // Khoảng cách giữa hai bánh xe
float vantoc = 0;
volatile unsigned long count = 0;
unsigned long count_prev = 0;
float Theta_now1; 
float Theta_prev1 = 0;
float Theta_now2; 
float Theta_prev2 = 0;
float Vl_output;
float RPM_output1, RPM_input1;
float Vr_output;
float RPM_output2, RPM_input2;
float dt1;  
float dt2;                     
 
unsigned long t_prev = 0;
unsigned long t_now1;
unsigned long t_prev1 = 0;
unsigned long t_now2;
unsigned long t_prev2 = 0;
volatile long dem_motor1 = 0;
volatile long dem_motor2 = 0;
volatile long dem_motor11 = 0;
volatile long dem_motor22 = 0;
volatile long dem_motor111 = 0;
volatile long dem_motor222 = 0;
int PWMval1 = 0;
int PWMval2 = 0;
const float Vmax = 24;      
const float Vmin = 0;
float V1 = 0;
float V2 = 0;
float globalVL = 0;
float globalVR = 0;
float globalVLL = 0;
float globalVRR = 0;
float v = 0, w = 0;
unsigned long prevTime = 0;
float leftWheelSpeedpre = 0;
float rightWheelSpeedpre = 0;
float omega = 0.3;
float R = 125;
float t = 0;
const float b = 0.03;
float Kx = 1.15, Ky = 2.1, Kth = 1.2;
const float pi = 3.14159265359;
const float d = 0.2;
bool check = false;

WebServer server(80); 

// Hàm ngắt xử lý encoder motor 1
void IRAM_ATTR dem_xung_motor1() {
  if (digitalRead(encoB_motor1) == HIGH) {
    dem_motor1++;
    dem_motor11++;
  } else {
    dem_motor1++;
    dem_motor11--;
  }
}

// Hàm ngắt xử lý encoder motor 2
void IRAM_ATTR dem_xung_motor2() {
  if (digitalRead(encoB_motor2) == HIGH) {
    dem_motor2++;
    dem_motor22++;
  } else {
    dem_motor2++;
    dem_motor22--;
  }
}

// Hàm ngắt timer
void IRAM_ATTR onTimer1() {
  count++;
}

void setup() {
  Serial.begin(56000); 
  
  // Cấu hình pins động cơ
  pinMode(motor1Pin1, OUTPUT);
  pinMode(motor1Pin2, OUTPUT);
  pinMode(enable1Pin, OUTPUT);
  pinMode(motor2Pin1, OUTPUT);
  pinMode(motor2Pin2, OUTPUT);
  pinMode(enable2Pin, OUTPUT);
  
  // Cấu hình PWM
  ledcSetup(pwmChannel, freq, resolution);
  ledcSetup(pwmChannel + 1, freq, resolution);
  ledcAttachPin(enable1Pin, pwmChannel);
  ledcAttachPin(enable2Pin, pwmChannel + 1);

  // Cấu hình encoder
  pinMode(encoA_motor1, INPUT);
  pinMode(encoB_motor1, INPUT);
  pinMode(encoA_motor2, INPUT);
  pinMode(encoB_motor2, INPUT);
  attachInterrupt(digitalPinToInterrupt(encoA_motor1), dem_xung_motor1, RISING);
  attachInterrupt(digitalPinToInterrupt(encoA_motor2), dem_xung_motor2, RISING);
  
  // Cấu hình timer
  timer1 = timerBegin(0, 80, true); 
  timerAttachInterrupt(timer1, &onTimer1, true); 
  timerAlarmWrite(timer1, 150000, true); 
  timerAlarmEnable(timer1); 

  // Kết nối WiFi
  WiFi.begin(ssid, password);
  while (WiFi.status() != WL_CONNECTED) {
    Serial.println("Connecting to WiFi...");
  }

  Serial.println("WiFi connected");
  Serial.print("IP address: ");
  Serial.println(WiFi.localIP());

  // Cấu hình server
  server.on("/", handleRoot);
  server.on("/start", handleStart);
  server.on("/stop", stop);

  server.begin();
  Serial.println("HTTP server started");
  Serial.println("CLEARDATA"); // Xóa tất cả dữ liệu Excel
  Serial.println("LABEL,Date,Time,t,x,y,ex,ey,eth,vd,wd,vt,wt");
}

void loop() {
  server.handleClient();
  tinhtoado();

  // Dừng động cơ nếu không có tín hiệu
  if(globalVLL == 0) {
    ledcWrite(pwmChannel + 1, 0);
  }
  if(globalVRR == 0) {
    ledcWrite(pwmChannel, 0);
  }
  
  // Xử lý khi có tín hiệu timer
  if (count > count_prev) {
    // Ghi dữ liệu đến Excel nếu t nằm trong khoảng hợp lệ
    if(t > 0.01 && t < 30.1) {
      sendDataToExcel();
    }
    
    quydao();
    
    // Tính toán thời gian
    t_now1 = millis();
    t_now2 = millis();
    dt1 = (t_now1 - t_prev1);
    dt2 = (t_now2 - t_prev2);
    
    // Thực hiện PID
    PID1();
    PID2();
    
    // Cập nhật vận tốc thực
    robot.vthuc = (Vl_output + Vr_output) / 2;
    robot.wthuc = (Vr_output - Vl_output) / l;
    
    // Cập nhật thời gian trước đó
    t_prev1 = t_now1;
    t_prev2 = t_now2;
    count_prev = count;
  }
}

// Hàm gửi dữ liệu đến Excel
void sendDataToExcel() {
  Serial.print("DATA,DATE,TIME,"); 
  Serial.print(t); 
  Serial.print(",");
  Serial.print(robot.toadox); 
  Serial.print(",");
  Serial.print(robot.toadoy); 
  Serial.print(",");
  Serial.print(robot.ex * 100); 
  Serial.print(",");
  Serial.print(robot.ey * 100); 
  Serial.print(",");
  Serial.print(robot.eth); 
  Serial.print(",");
  Serial.print(traj.Vc); 
  Serial.print(",");
  Serial.print(traj.Wc); 
  Serial.print(",");
  Serial.print(robot.vthuc); 
  Serial.print(",");
  Serial.print(robot.wthuc); 
  Serial.println(",");
}

// Hàm tính toán tọa độ robot
void tinhtoado() {
  unsigned long currentTime = millis();
  float deltaTime = (currentTime - prevTime) / 1000.0;
  
  // Tính toán vận tốc bánh xe
  float leftWheelSpeed = (dem_motor22 / 249.6) * pi * d;
  float rightWheelSpeed = (dem_motor11 / 249.6) * pi * d;
  
  // Tính toán v và w
  v = (rightWheelSpeed + leftWheelSpeed) / 2;
  w = (rightWheelSpeed - leftWheelSpeed) / l;
  
  // Cập nhật vị trí robot
  robot.theta = robot.theta + w;
  robot.x = robot.x + v * cos(robot.theta + (w / 2));
  robot.y = robot.y + v * sin(robot.theta + (w / 2));

  robot.toadox = robot.x * 100;
  robot.toadoy = robot.y * 100;
  
  // Reset bộ đếm encoder
  dem_motor11 = 0;
  dem_motor22 = 0;
  prevTime = currentTime;
}
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
